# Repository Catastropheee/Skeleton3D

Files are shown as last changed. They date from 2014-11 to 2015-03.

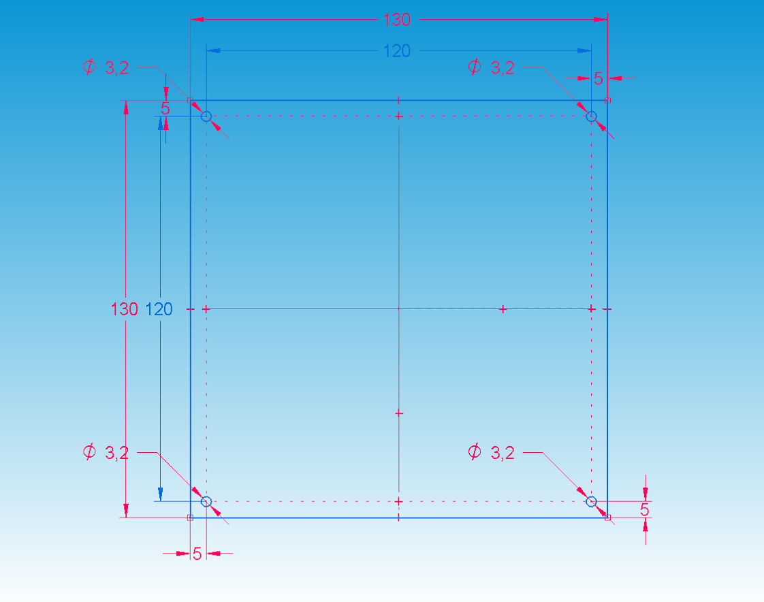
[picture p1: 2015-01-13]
STL Skeleton3D/Wood_Steel plate/Wood_Steel plate.png

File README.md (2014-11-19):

Skeleton3D
==========

Source de la petite reprap française 
Je viens vous présenter mon petit projet reprap: la skeleton 3D

L’idée a germé dans ma tête après quelques mois d’utilisation de ma prusa i3, beaucoup de personnes dans mon entourage avaient envie de voir la bécane fonctionner mais ce n’est pas super facile de transporter une i3. De plus, j’ai constaté que j’utilisais très rarement l’entière surface d’impression et que la majorité de mes print se limite à une surface de 100x100.

Après avoir cherché une petite imprimante compacte, transportable et peu chère sur le wiki, j’ai décidé d’en concevoir une répondant à mes besoins faute d’en trouver une ! 
C’est-à-dire: transportable, robuste, évolutive, peu cher mais avec des impressions de qualité !

L'union faisant la force et augmentant la créativité, j’ai travaillé avec un ami possédant aussi une i3 qui a tout de suite accroché.

Nous avons par la suite, commencé par définir :
L’architecture de la machine 
- Pièces plastiques + tiges filetés Ø8 (?€)
- Déplacement de la hotend en X et Y (course 100x100) et du plateau en Z (course 100 à 150 mm)
- Mouvements axiaux + Extrusion
- 4 moteurs NEMA 17 de 40 mm et 4kg
- 1 extruder conçu pour être compact et en directdrive

Guidage axiaux :
- Classique avec des LM8UU

Hotend :
- Aluhotend 1.75mm (en cours de test)

Alimentation :
- 72W de pc portable

Améliorations apportées au prototype :
->	Augmentation de la surface de guidage (2xLM8uu) au niveau de l’effort moteur (X et Y) pour supprimer le risque d’arc boutement
->	Augmentation de la surface de guidage du plateau Z (3x LM8uu) pour limiter la flexion
->	Augmentation de la surface de guidage de la hotend (4 x LM8uu) pour supprimer les jeux
->	Mise en place d’un plateau acier galva 15/10
->	Fixation par vis des endstop intégré aux pièces plastiques
->	Calibrage Z via une vis M4 réglable

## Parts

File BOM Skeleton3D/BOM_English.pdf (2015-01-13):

N° | Qty. | STL files ?
1 | 8 | N° | Qty. | STL files ? | N° | Qty. | STL files ?
2 | 2 | 1 | 1 | .stl | 1 | 3
3 | 1 | 2 | 1 | | 2 | 1 | .stl
4 | 3 | 3 | 1 | .stl | 3 | 1
5 | 1 | 4 | 1 | | 4 | 1 | .stl
6 | 4 | .stl | 5 | 1 | .stl
7 | 1 | .stl | 6 | 2
8 | 1 | .stl | 7 | 1
9 | 1 | .stl | 8 | 3
10 | 4 | .stl | 9 | 1
11 | 4 | 10 | 1
12 | 4 | 11 | 1
13 | 1 | .stl | 12 | 1
14 | 1 | .stl | 13 | 1
15 2
16 2
17 | 2 | N° | Qty. | STL files ?
18 | 1 | .stl | 1 | 2
19 | 55 | 2 | 3
20 | 1 | .stl | 3 | 1
21 | 1 | 4 | 1 | .stl
22 | 3 | 5 | 1
23 22 | | Socket cap screw - M3x10
24 6 | | Socket cap screw - M3x20
25 10 | | M3 nuts
26 1 | | Steel plate
27 1 | | Ramps 1.4/Arduino
28 | 4 | Ramps tab | .stl
29 2 | | Sous-ensemble glissière (see Page 2)
30 | 1 | Support hotend | .stl
31 1 | | Sous-ensemble Extruder (See page 3)
32 3 | | M4 nuts
33 | 1 | Mouting clip motor E | .stl
34 1 | | Socket cap screw - M4x10
35 | 1 | Belt guidance X | .stl
36 | 1 | Belt guidance Y | .stl
37 5 | | Socket cap screw - M3x30
38 1 | | Socket cap screw - M3x40
39 1 | | Long M5 nuts
40 11 | | M3 nuts
41 1 | | Fan 40x40x10
42 1 | | Fan 30x30x10
43 | 1 | Bec cooling | .stl
44 2 | | Inductive sensor M8 - 2mm detection
45 2 | | M8 nuts
46 | 1 | Z_support_plate_link | .stl
47 | 1 | Z_left_support_plate | .stl
48 | 1 | Z_right_support_plate | .stl
49 | 1 | Plate_pusher | .stl
50 1 | | Socket cap screw - M4x10
51 8 | | LM8UU
52 4 | | Tie wrap
53 | 2 | Steel/PLA triangle | .stl

NEMA 17 - 4kg torque - 40mm GT2 pulley
624zz bearing
GT2 belt - 800mm to be sure Support pulley Y
M8 nuts
Support motor X

Z_top_connector

Name

NEMA 17 - 4kg torque - 40mm Wood plate
Bottom connector
Z_motor_piece_1_2
Z_motor_piece_2_2

Top connector

Shaft coupling 5x5

Ø8 Smooth Rod - 220mm
M8 Threaded Rod - 190mm
Support motor Y
Support pulley X

Page 1

M8 Threaded Rod - 240mm | Name
Ø8 Smooth Rod - 180mm
M5 Threaded Rod - 160mm

Microswitch mechanical - 20x10mm

Aluhotend (http://reprap.org/wiki/Aluhotend)

Compact Extrudeur 1.75
Sous-ensemble Entrainement (see behind) Geared wheels
624zz bearings
Mobile party
M3 nuts

Name

M5x30 Hex screw

605zz bearings
Washer M5
MK7
Geared wheels

USE IT WITH BOM_Skeleton3D.pdf

Sous-ensemble Entrainement

Page 3
Sous-ensemble 31 : Extrudeur

Page 2
Sous-ensemble 29 : Glissière Name
LM8UU
Opposite linear guidance
Ø8 Smooth rods - 220mm
Motor linear guidance

Socket cap screw - M3x20
Socket cap screw - M3x10
Socket cap screw - M4x10
M4 nuts
Socket cap screw - M3x40

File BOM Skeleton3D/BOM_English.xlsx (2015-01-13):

USE IT WITH BOM_Skeleton3D.pdf
Page 1 |  |  |  | Page 3 |  |  |  | Page 2
N° | Qty. | Name | STL files ? | Sous-ensemble 31 : Extrudeur |  |  |  | Sous-ensemble 29 : Glissière
1 | 8 | M8 Threaded Rod - 240mm |  | N° | Qty. | Name | STL files ? | N° | Qty. | Name | STL files ?
2 | 2 | Ø8 Smooth Rod - 180mm |  | 1 | 1 | Compact Extrudeur 1.75 | .stl | 1 | 3 | LM8UU
3 | 1 | M5 Threaded Rod - 160mm |  | 2 | 1 | Sous-ensemble Entrainement (see behind) |  | 2 | 1 | Opposite linear guidance | .stl
4 | 3 | NEMA 17 - 4kg torque - 40mm |  | 3 | 1 | Geared wheels | .stl | 3 | 1 | Ø8 Smooth rods - 220mm
5 | 1 | Wood plate |  | 4 | 1 | 624zz bearings |  | 4 | 1 | Motor linear guidance | .stl
6 | 4 | Bottom connector | .stl | 5 | 1 | Mobile party | .stl
7 | 1 | Z_motor_piece_1_2 | .stl | 6 | 2 | M3 nuts
8 | 1 | Z_motor_piece_2_2 | .stl | 7 | 1 | Socket cap screw - M3x20
9 | 1 | Z_top_connector | .stl | 8 | 3 | Socket cap screw - M3x10
10 | 4 | Top connector | .stl | 9 | 1 | Socket cap screw - M4x10
11 | 4 | Ø8 Smooth Rod - 220mm |  | 10 | 1 | M4 nuts
12 | 4 | M8 Threaded Rod - 190mm |  | 11 | 1 | Socket cap screw - M3x40
13 | 1 | Support motor Y | .stl | 12 | 1 | Aluhotend (http://reprap.org/wiki/Aluhotend)
14 | 1 | Support pulley X | .stl | 13 | 1 | NEMA 17 - 4kg torque - 40mm
15 | 2 | GT2 pulley
16 | 2 | 624zz bearing |  | Sous-ensemble Entrainement
17 | 2 | GT2 belt - 800mm to be sure |  | N° | Qty. | Name | STL files ?
18 | 1 | Support pulley Y | .stl | 1 | 2 | 605zz bearings
19 | 55 | M8 nuts |  | 2 | 3 | Washer M5
20 | 1 | Support motor X | .stl | 3 | 1 | MK7
21 | 1 | Shaft coupling 5x5 |  | 4 | 1 | Geared wheels | .stl
22 | 3 | Microswitch mechanical - 20x10mm |  | 5 | 1 | M5x30 Hex screw
23 | 22 | Socket cap screw - M3x10
24 | 6 | Socket cap screw - M3x20
25 | 10 | M3 nuts
26 | 1 | Steel plate
27 | 1 | Ramps 1.4/Arduino
28 | 4 | Ramps tab | .stl
29 | 2 | Sous-ensemble glissière (see Page 2)
30 | 1 | Support hotend | .stl
31 | 1 | Sous-ensemble Extruder (See page 3)
32 | 3 | M4 nuts
33 | 1 | Mouting clip motor E | .stl
34 | 1 | Socket cap screw - M4x10
35 | 1 | Belt guidance X | .stl
36 | 1 | Belt guidance Y | .stl
37 | 5 | Socket cap screw - M3x30
38 | 1 | Socket cap screw - M3x40
39 | 1 | Long M5 nuts
40 | 11 | M3 nuts
41 | 1 | Fan 40x40x10
42 | 1 | Fan 30x30x10
43 | 1 | Bec cooling | .stl
44 | 2 | Inductive sensor M8 - 2mm detection
45 | 2 | M8 nuts
46 | 1 | Z_support_plate_link | .stl
47 | 1 | Z_left_support_plate | .stl
48 | 1 | Z_right_support_plate | .stl
49 | 1 | Plate_pusher | .stl
50 | 1 | Socket cap screw - M4x10
51 | 8 | LM8UU
52 | 4 | Tie wrap
53 | 2 | Steel/PLA triangle | .stl

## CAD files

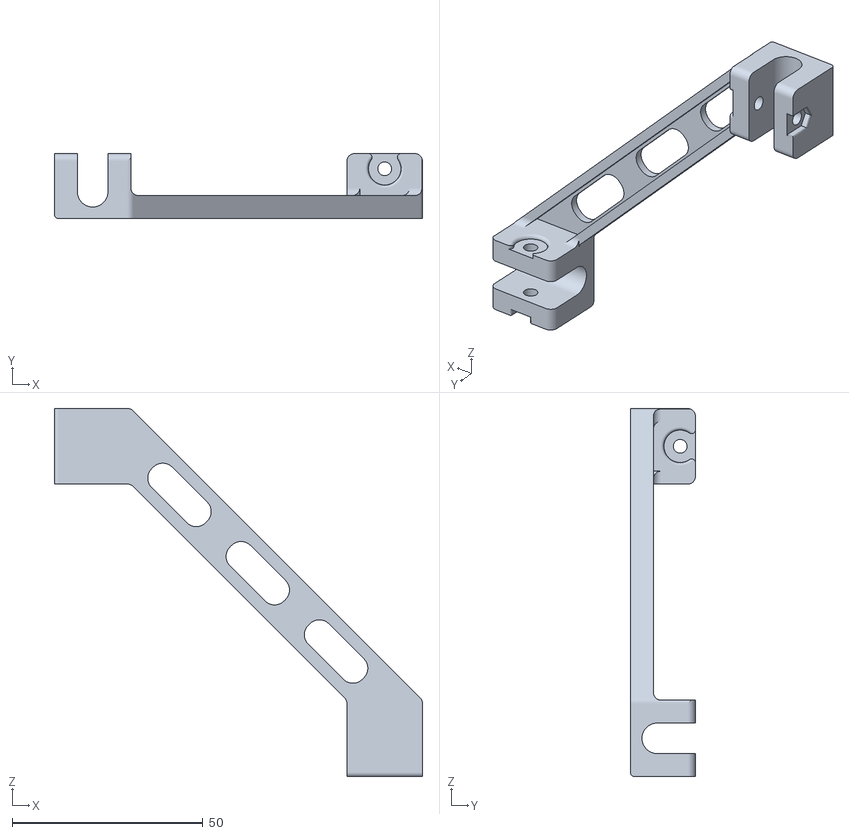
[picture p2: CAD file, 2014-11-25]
STL Skeleton3D/PLA triangle/PLA triangle.stl
96.4 x 17.0 x 96.4

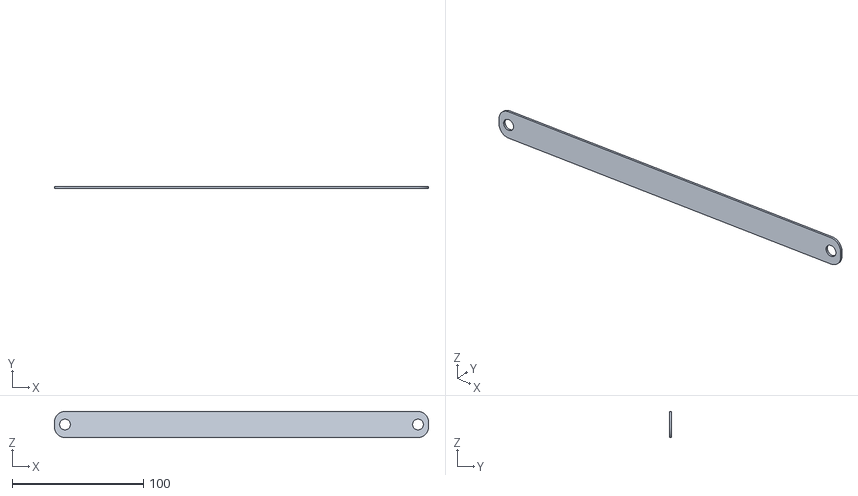
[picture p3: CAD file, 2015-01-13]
STL Skeleton3D/Steel triangle/Steel triangle.stl
285.0 x 1.50 x 20.0

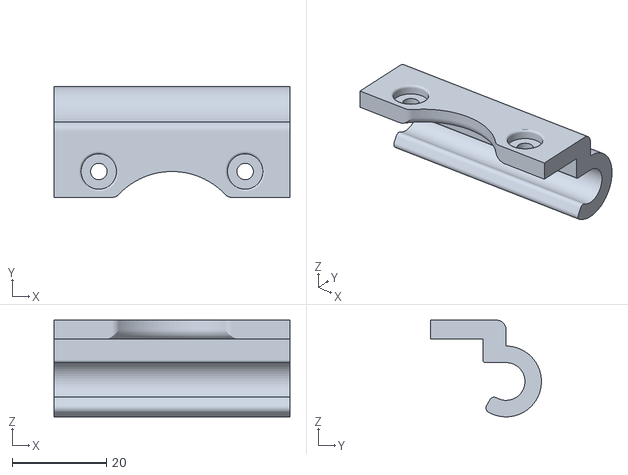
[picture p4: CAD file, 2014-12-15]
STL Skeleton3D/STL axe Z/Z_motor_piece_2_2.stl
50.0 x 23.5 x 20.5

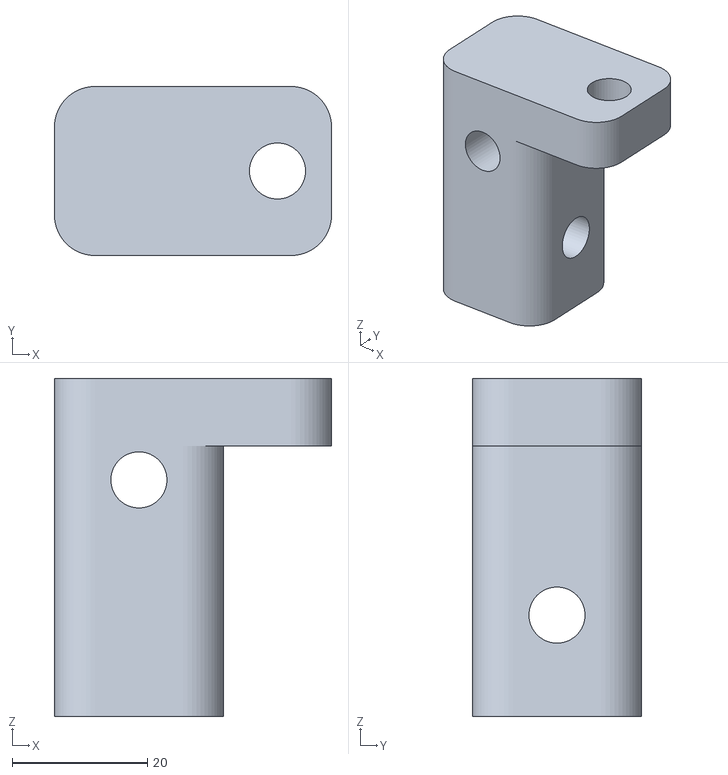
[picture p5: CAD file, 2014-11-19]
STL Skeleton3D/STL connectors/Bottom connector.stl
41.0 x 25.0 x 50.0

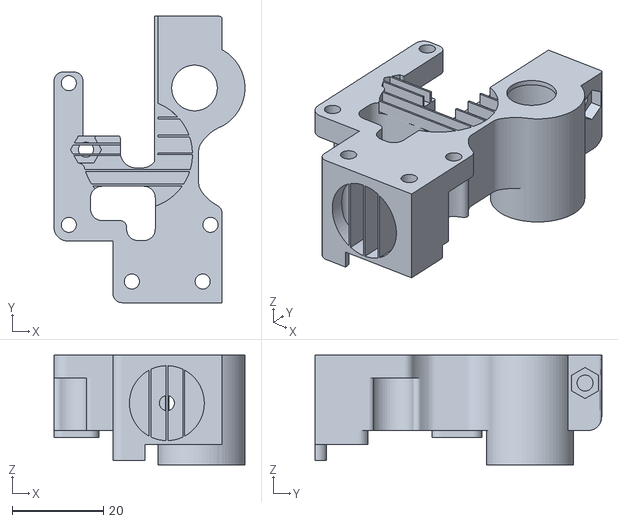
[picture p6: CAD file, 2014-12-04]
STL Skeleton3D/STL Extrudeur/Extrudeur pour thingiverse/Compact Extruder Ø3mm only with support.stl
41.8 x 62.7 x 24.0

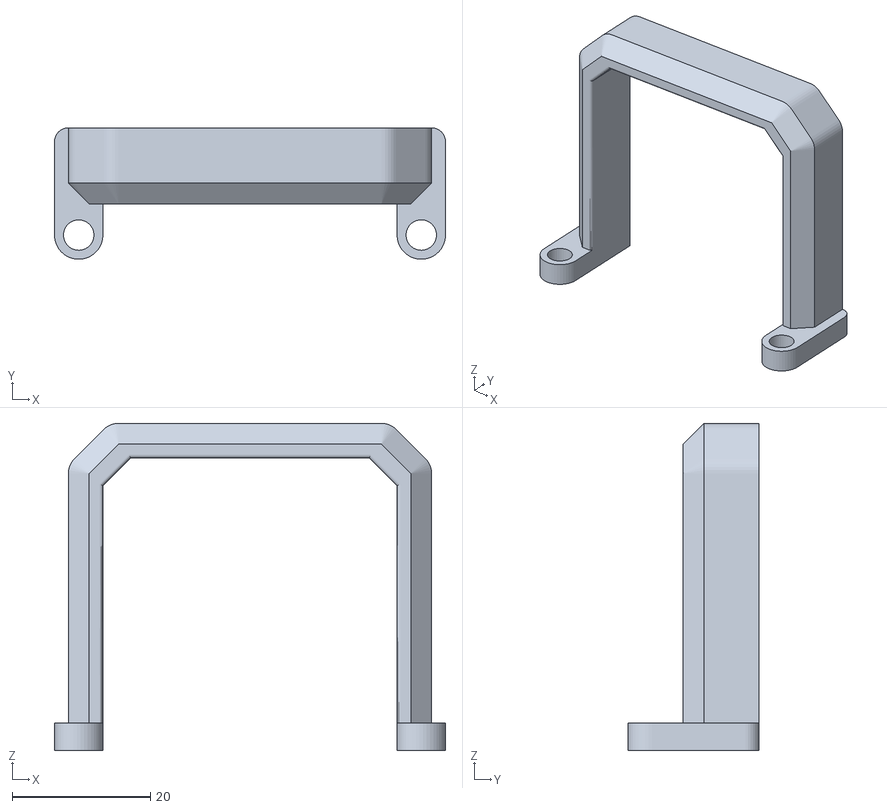
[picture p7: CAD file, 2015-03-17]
STL Skeleton3D/STL Extrudeur/Mouting clip motor E.stl
56.5 x 19.0 x 47.3

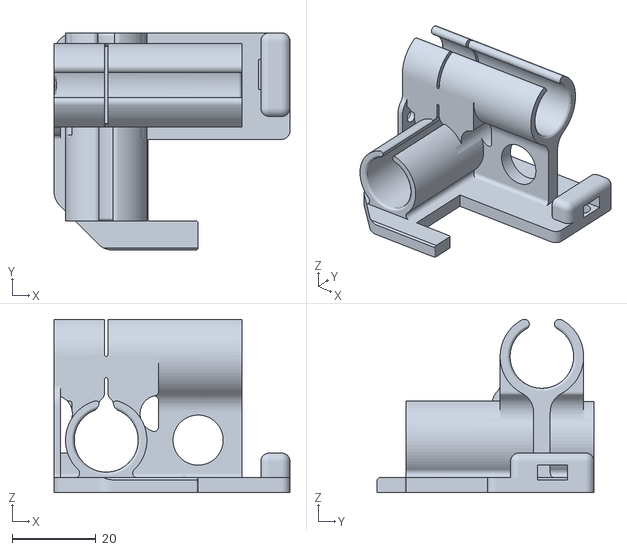
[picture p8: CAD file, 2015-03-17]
STL Skeleton3D/Support hotend.stl
56.5 x 52.0 x 41.5

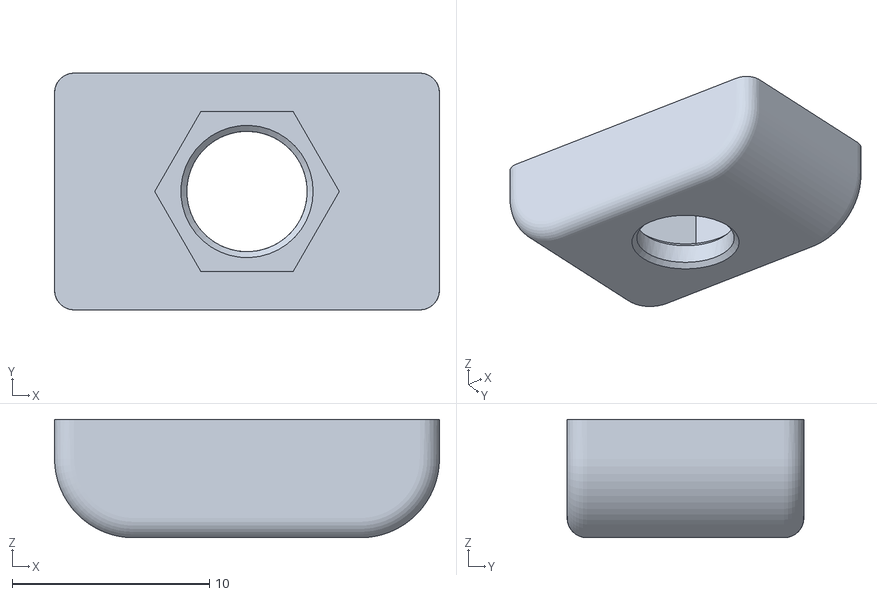
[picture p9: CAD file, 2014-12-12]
STL Skeleton3D/STL axe Z/Plate_pusher.stl
19.5 x 12.0 x 6.00

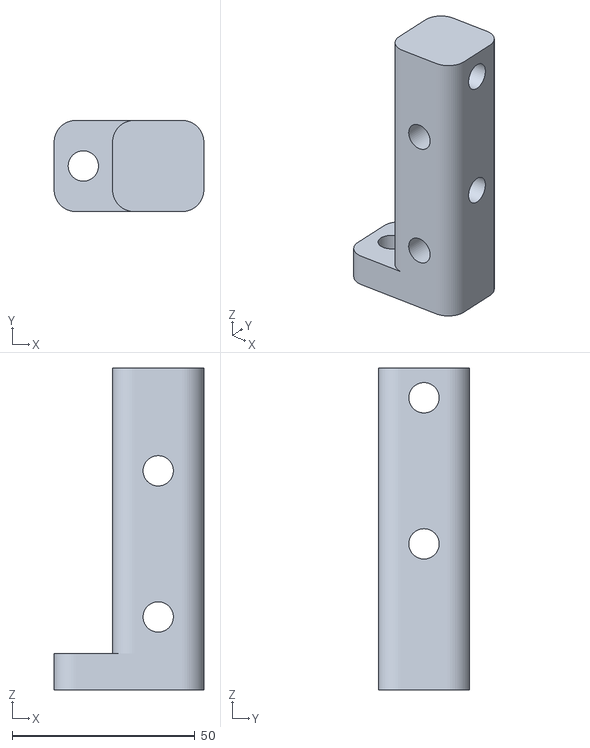
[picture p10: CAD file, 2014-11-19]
STL Skeleton3D/STL connectors/Top connector.stl
41.0 x 25.0 x 88.2

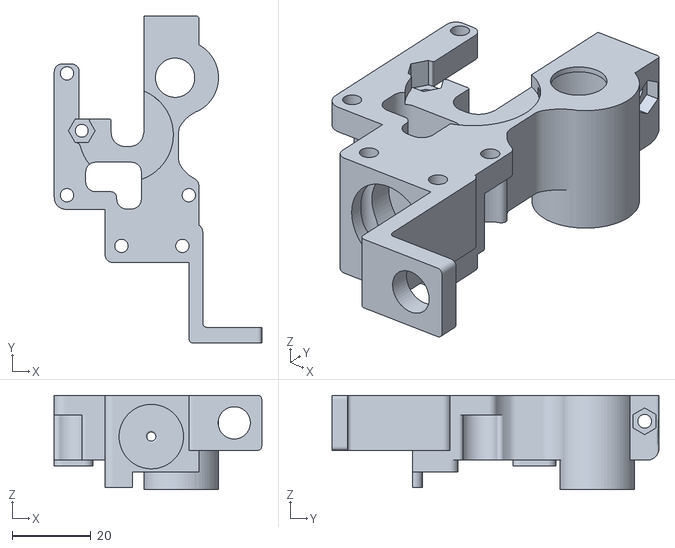
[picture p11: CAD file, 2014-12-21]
STL Skeleton3D/STL Extrudeur/Compact Extruder 1.75 without support.stl
52.8 x 83.2 x 24.0

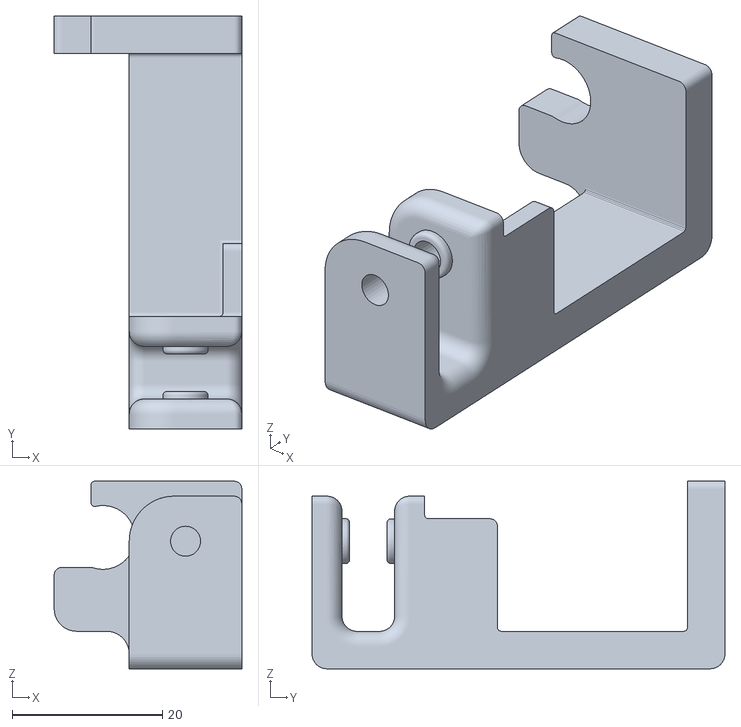
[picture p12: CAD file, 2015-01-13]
STL Skeleton3D/Support pulley X.stl
25.0 x 55.0 x 25.0

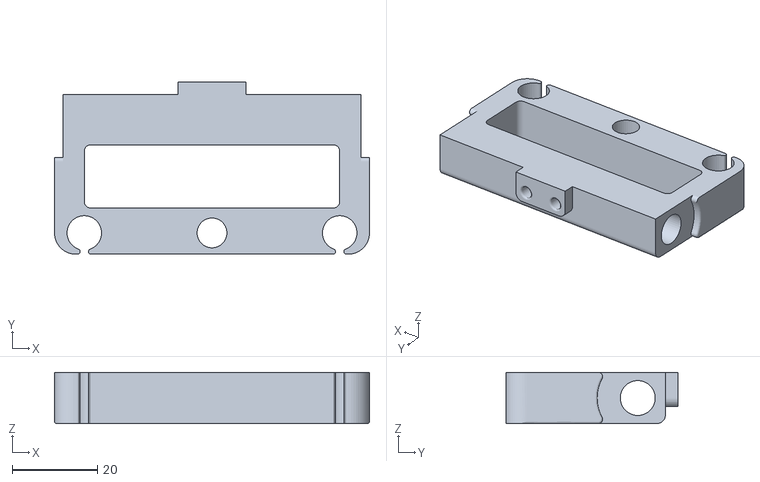
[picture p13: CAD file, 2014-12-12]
STL Skeleton3D/STL axe Z/Z_top_connector.stl
74.0 x 40.5 x 12.0

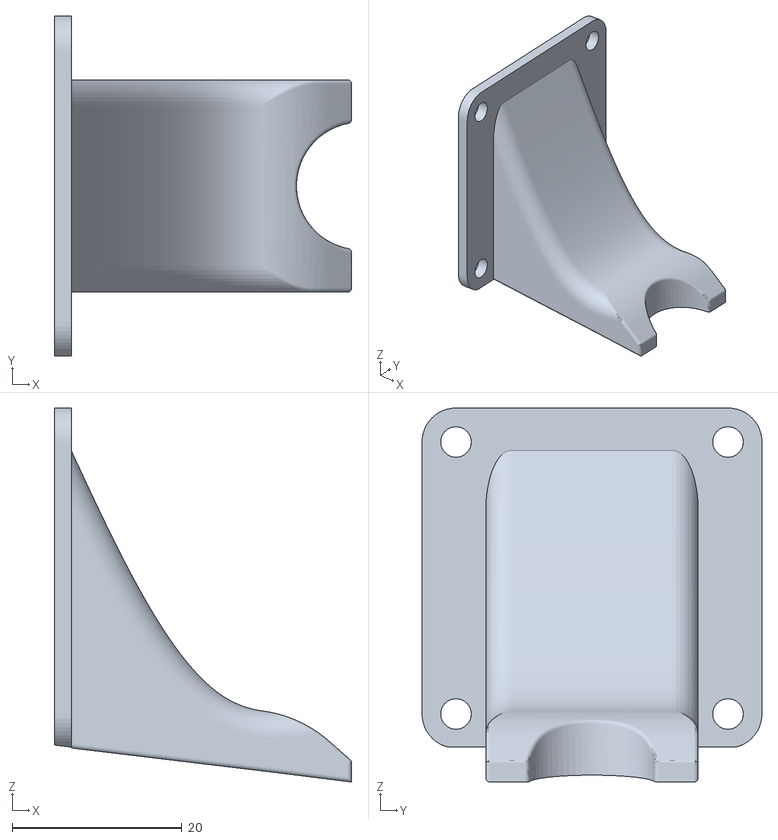
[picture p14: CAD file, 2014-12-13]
STL Skeleton3D/STL Extrudeur/Bec cooling.stl
35.0 x 40.0 x 44.0

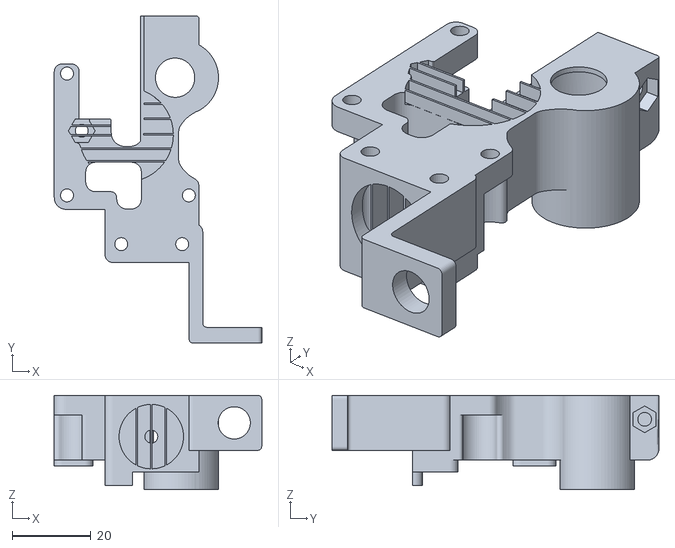
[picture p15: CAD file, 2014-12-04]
STL Skeleton3D/STL Extrudeur/Extrudeur pour thingiverse/Compact Extruder Ø3mm with sensor with support.stl
52.8 x 83.2 x 24.0

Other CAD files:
STL Skeleton3D/STL Extrudeur/Extrudeur pour thingiverse/Compact Extruder Ø1.75mm only with support.stl
STL Skeleton3D/Support pulley Y.stl
STL Skeleton3D/Opposite linear guidance.stl
STL Skeleton3D/STL axe Z/Z_support_plate_link.stl
STL Skeleton3D/Belt guidance X.stl
STL Skeleton3D/Belt guidance Y.stl
STL Skeleton3D/Motor linear guidance.stl
STL Skeleton3D/Ramps tab.stl
STL Skeleton3D/STL Extrudeur/Extrudeur pour thingiverse/Compact Extruder Ø1.75mm with sensor with support.stl
STL Skeleton3D/STL Extrudeur/Geared wheels.stl
STL Skeleton3D/STL Extrudeur/Mobile party.stl
STL Skeleton3D/STL axe Z/Z_left_support_plate.stl
STL Skeleton3D/STL axe Z/Z_motor_piece_1_2.stl
STL Skeleton3D/STL axe Z/Z_right_support_plate.stl
STL Skeleton3D/Steel triangle/Steel triangle.dxf
STL Skeleton3D/Support motor X.stl
STL Skeleton3D/Support motor Y.stl

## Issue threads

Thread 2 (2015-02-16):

Wrong screw for extruder part 11?

crundy, 2015-02-16:
We're currently putting together a Skeleton3D, but noticed that an M4x10 screw is not long enough to fit through the part "Mobile party.stl". I did take photos but managed to lose them in a phone disaster, but if you measure the space in the STL file above you can see it's 11.5mm, and a M4 20 would be too long and would press against the motor.

Screencap: http://crundyjunk.s3.amazonaws.com/MobilePartyLength.png

Could you double check and see if either we're doing something wrong or if indeed the screw part number is wrong?

P.S. The part numbers for the extruder page do not match between the full BoM and the English translation spreadsheet (e.g. 11 in the BoM is the M4x10 screw above, but in the English BoM 11 is an M3x40). Minor issues but thought you should know.

Catastropheee, 2015-02-16:
Hi,

Thank you for your remark.
You're right, M4x10 is not the right screw for the "Mobile party". I use an
M4x16.

I will update the BOM soon!

2015-02-16 12:05 GMT+01:00 crundy <notifications@github.com>:

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

crundy, 2015-02-16:
Thanks!

Closed 2015-02-16.

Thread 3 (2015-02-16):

Unnecessary splitting of parts?

crundy, 2015-02-16:
Is there a particular reason why Plate_pusher.stl is separate from Z_support_plate_link.stl? lowering of the Z axis seems to by gravity only, as the plate pusher is not affixed to the Z support plate link, which generally wouldn't cause problems, but if a bearing got a stiff it could cause issues. Surely if you integrated the two parts so that the nut was fixed to the Z support plate link directly then you would have a more stable plate and less risk of the plate not lowering?

Catastropheee, 2015-02-16:
It has been designed to uncouple guidance and traction which normally cause wobble.

" but if a bearing got a stiff it could cause issues" Which bearing ?

crundy, 2015-02-16:
Fair enough. I haven't yet lined everything up properly so the Z axis is a little stiff, and so I was referring to the 4 bearings in the two Z support plates. Shouldn't be a problem once it's moving smoothly up and down. I'm guessing the weight of the wood and aluminium should suffice.

Closed 2015-02-16.

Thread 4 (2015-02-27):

Fans

crundy, 2015-02-27:
Apologies, quick couple of questions about the extruder fans:

1. Re "Bec cooling.stl", this seems to be [sitting extremely close to the nozzle and hotend](http://crundyjunk.s3.amazonaws.com/Fan.PNG). Are you sure it won't melt?
2. Why are the vents for the above pointing directly at the bed? Would this rapid cooling not cause layers to peel up?
3. I note there is only one bolt holding each fan in one of the corners. Are you sure this is stable enough and won't cause the fans to wobble or slip? Fan 41 looks like it could untighten slightly and start rubbing against the X-shaft, and fan 42 looks like it could flop and smack into the Bec cooling part. I can look into some ways of adding another bolt for one of the holes or something to rest the edge on the side of the CoG unless you think it's isn't an issue?
4. Was there any reason to use two different fan sizes? Would two of the same be fine?

Thanks again for the design. We're almost there with ours.

Catastropheee, 2015-03-04:
Hi,

1. It doesn't melt on my skeleton.

2. It's a good note. We need to improve this.

3. No problem with only one bolt. You can easily add a second bolt if you
want ;). Please share if you do it!

4. If we used a 40mm fan for the coldend we will loose 10mm print area!

2015-02-27 13:50 GMT+01:00 crundy <notifications@github.com>:

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

crundy, 2015-03-04:
1 & 2: OK, I'm going to leave this part off for now. I presume it isn't essential.
3: Yes you are correct, I attached the 30mm fan and it holds in place fine, although it does point downwards very slightly. Shouldn't be a problem though.
4: Yup, my bad.

Closed 2015-03-04.

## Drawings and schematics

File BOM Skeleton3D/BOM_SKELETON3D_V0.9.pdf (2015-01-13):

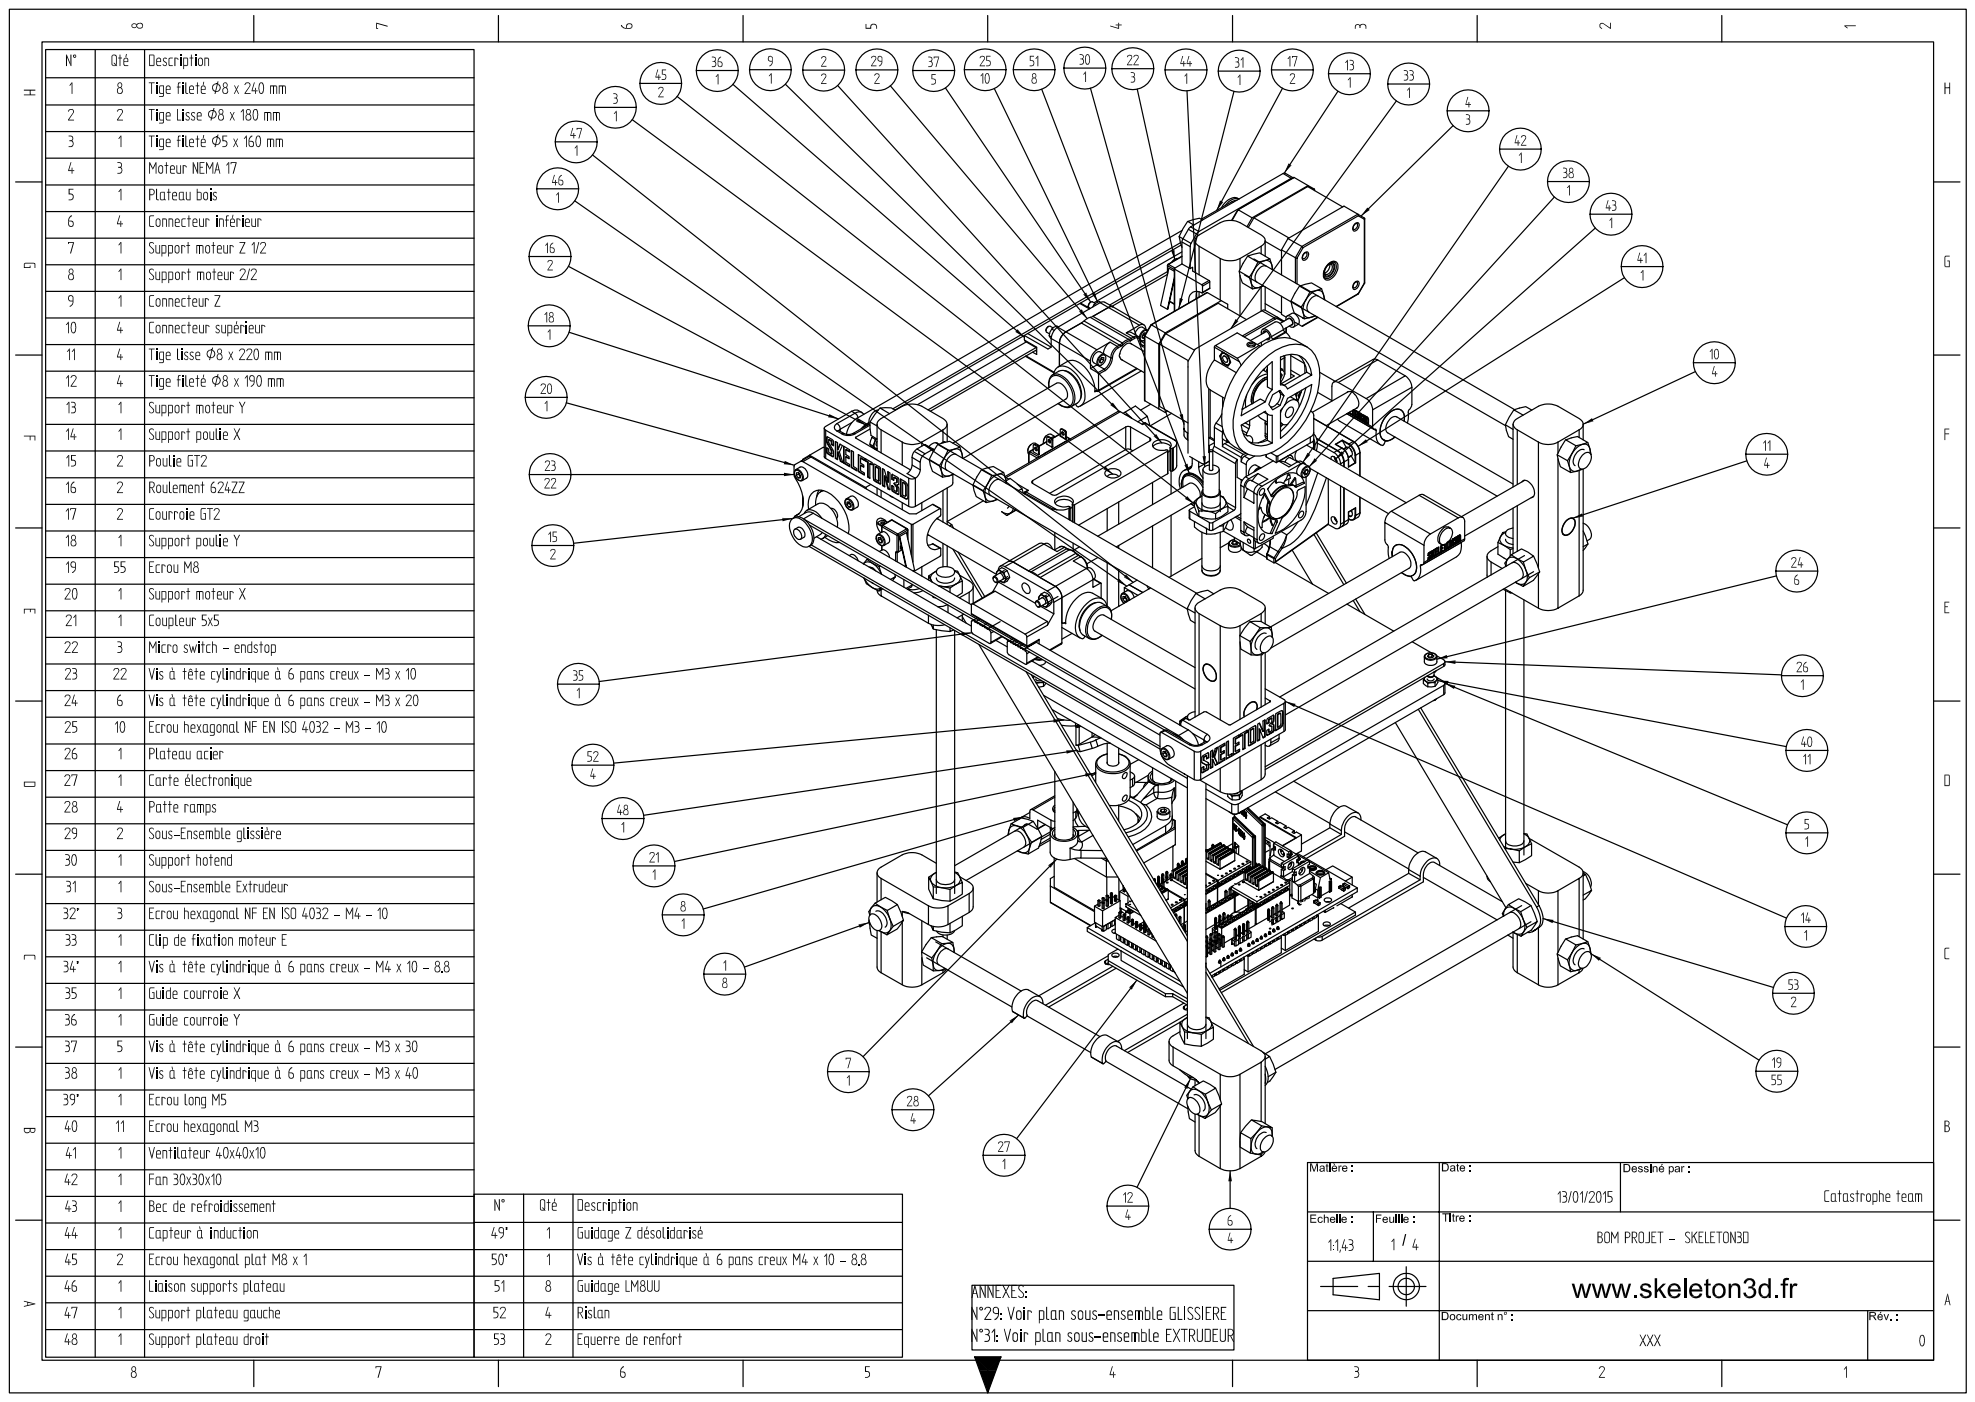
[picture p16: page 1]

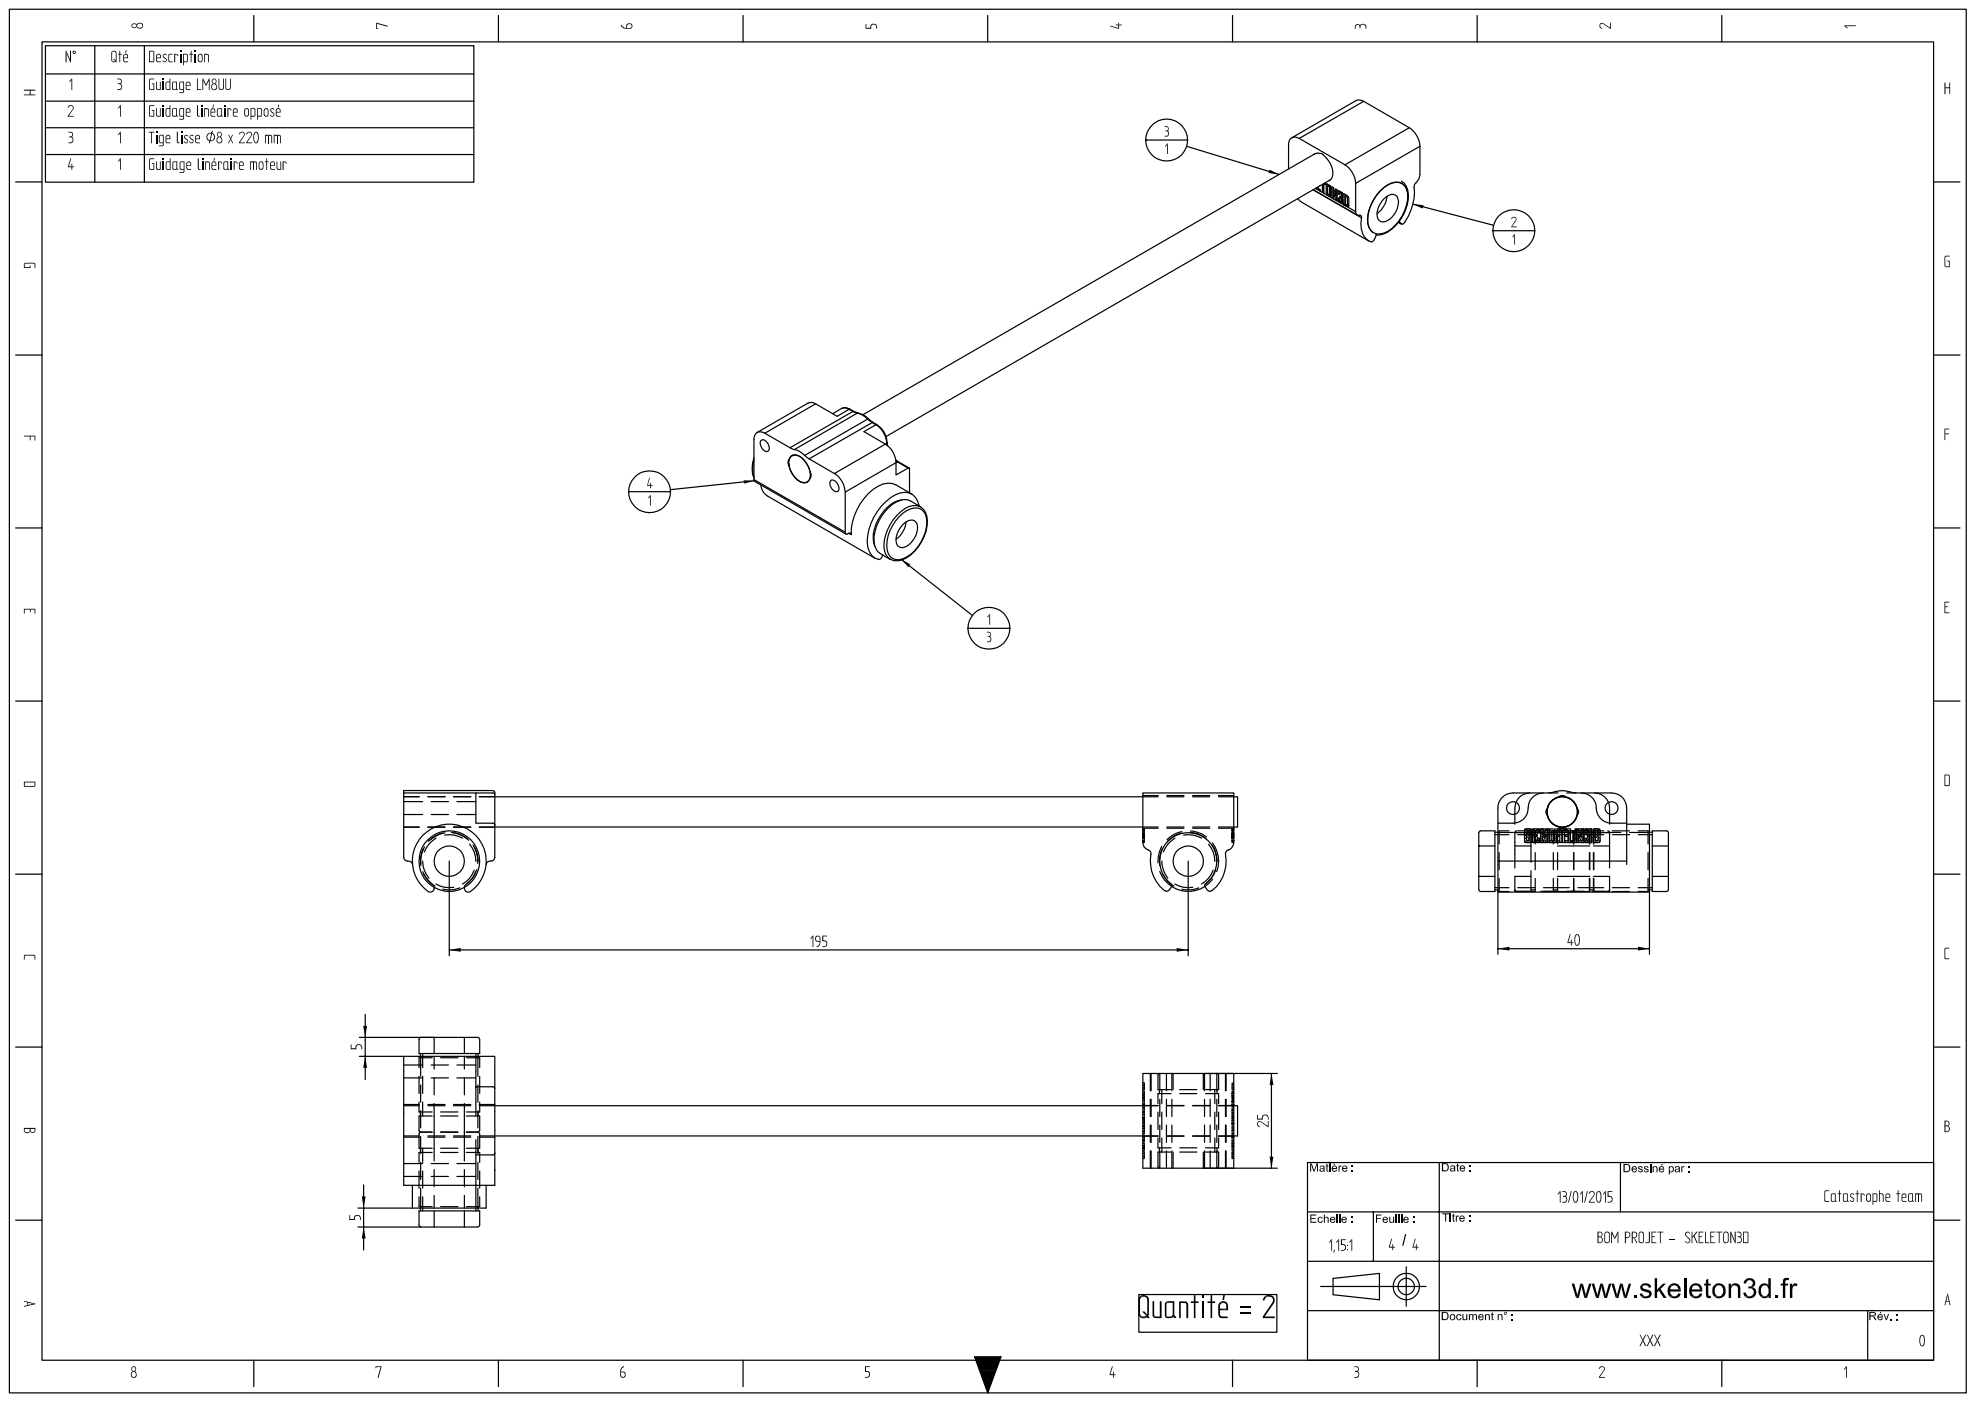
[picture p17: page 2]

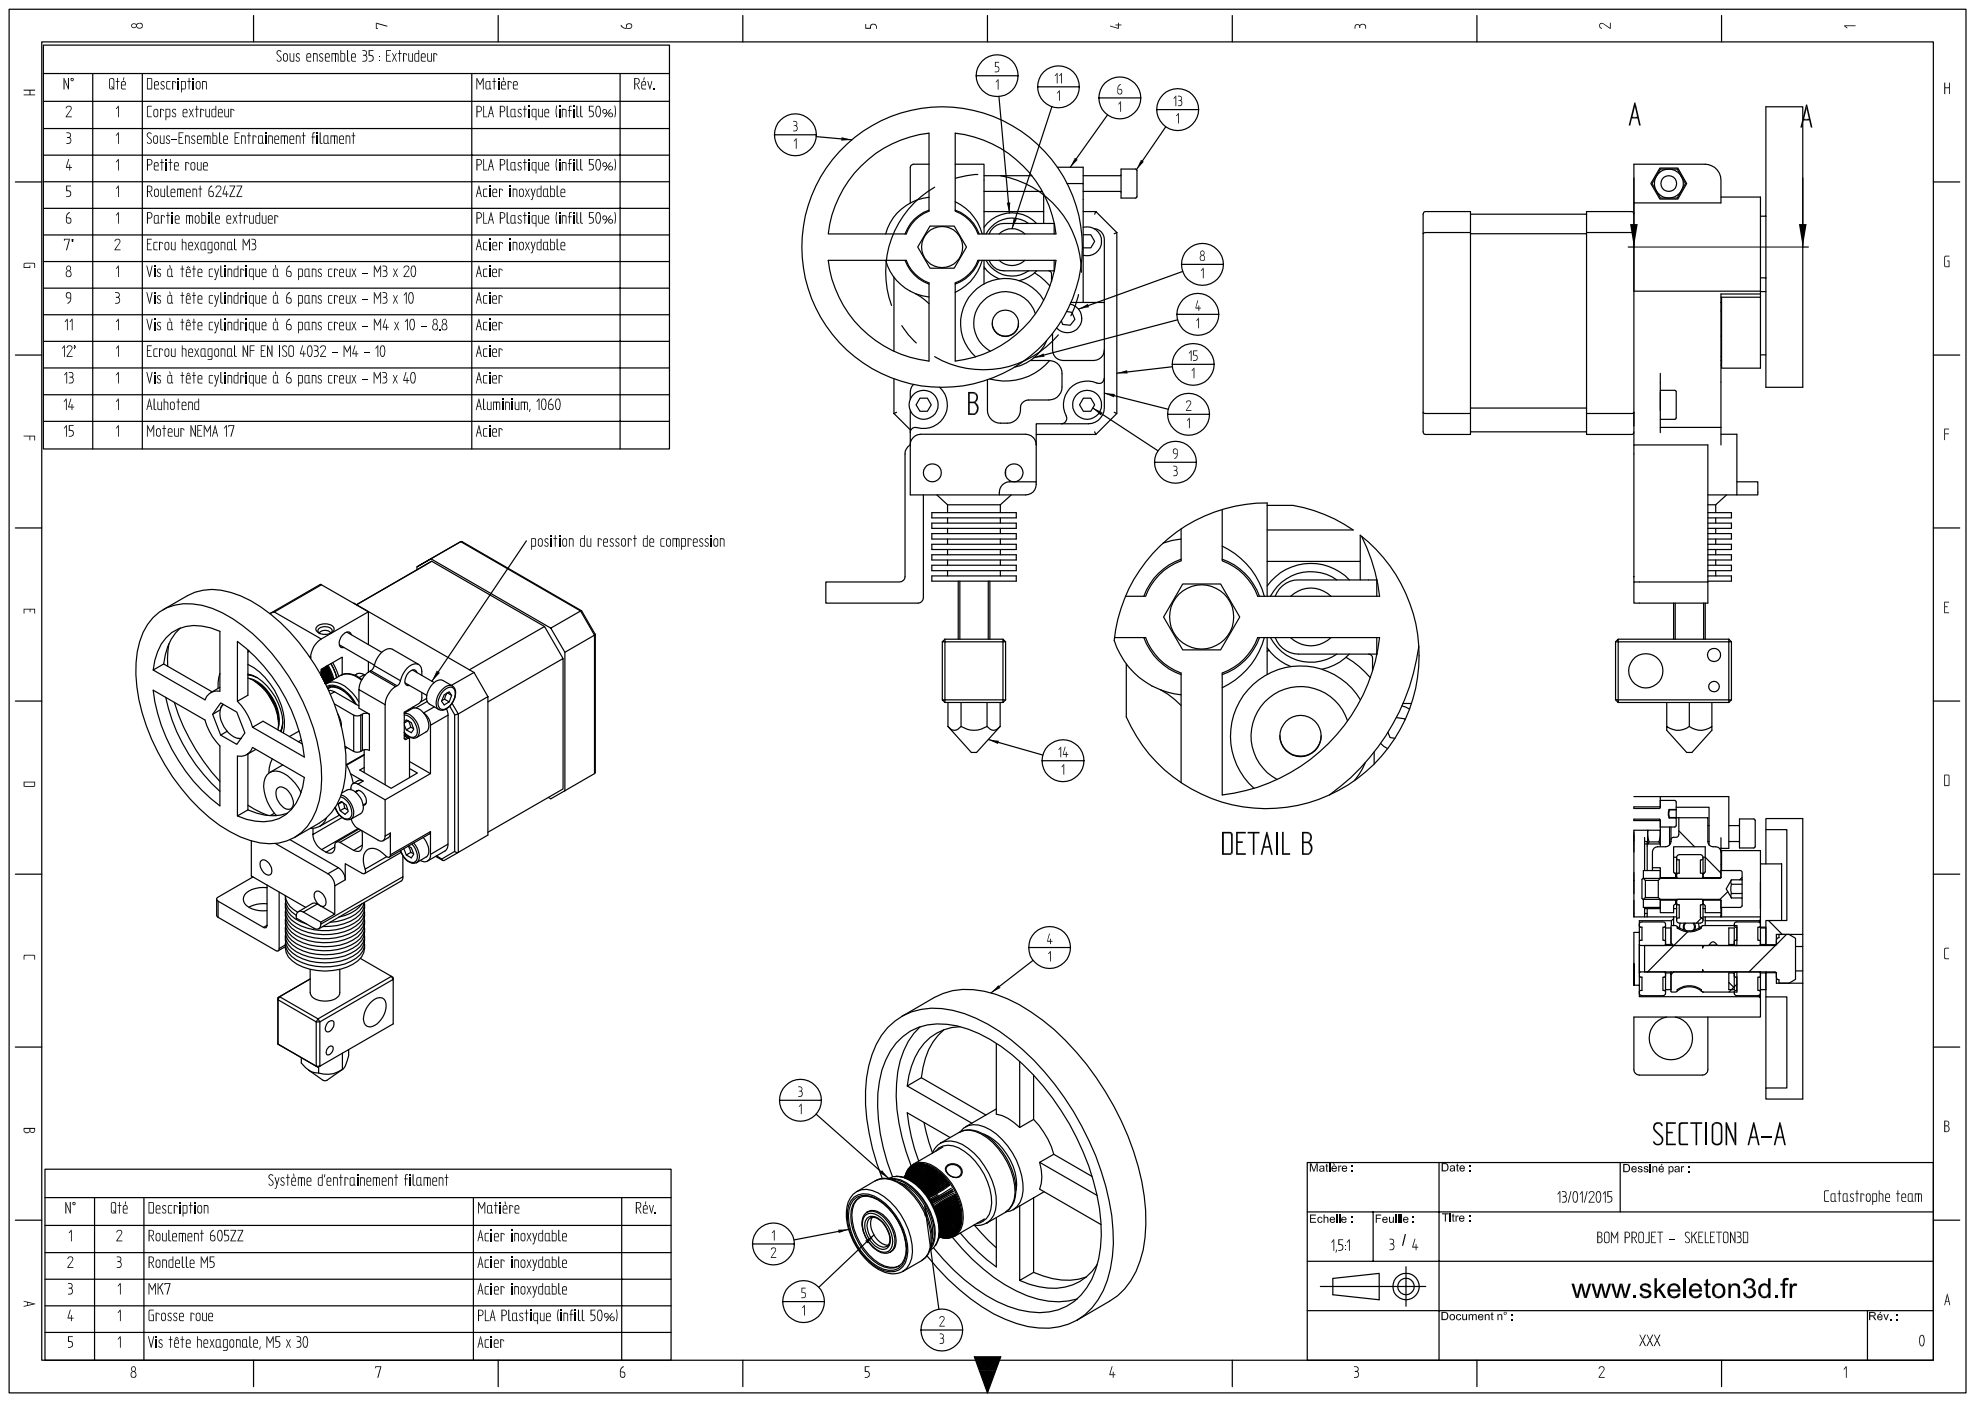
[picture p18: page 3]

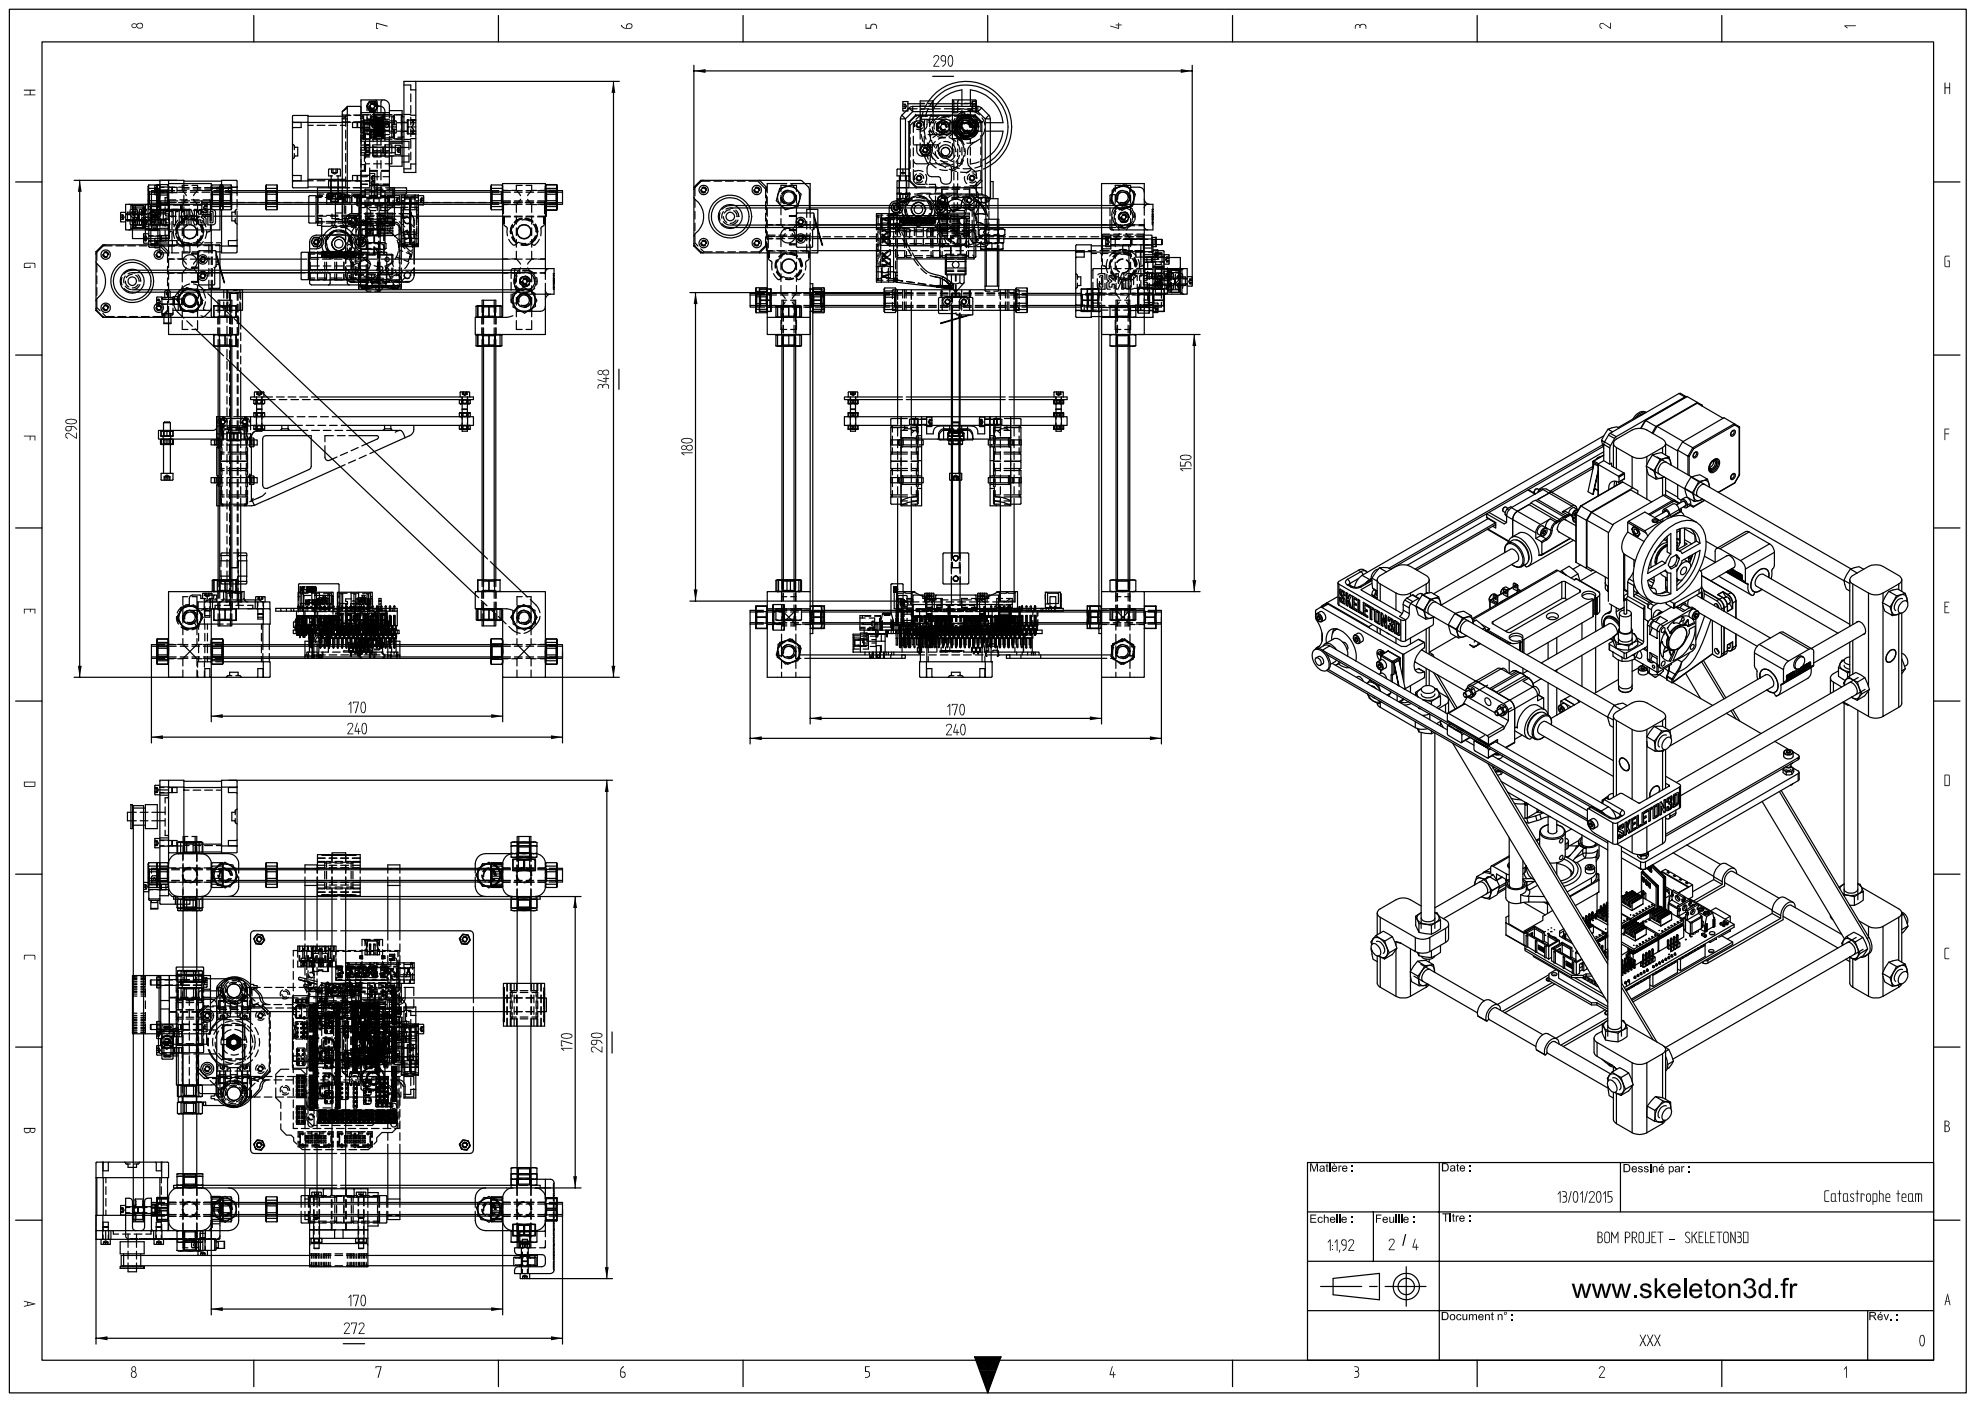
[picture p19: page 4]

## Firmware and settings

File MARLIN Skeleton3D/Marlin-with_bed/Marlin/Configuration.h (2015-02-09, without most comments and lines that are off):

#define CONFIGURATION_H
#define STRING_VERSION_CONFIG_H __DATE__ " " __TIME__ // build date and time
#define STRING_CONFIG_H_AUTHOR "(none, default config)" // Who made the changes.
#define SERIAL_PORT 0
#define BAUDRATE 250000
#define MOTHERBOARD 33
#define EXTRUDERS 1
#define POWER_SUPPLY 1
#define TEMP_SENSOR_0 10
#define TEMP_SENSOR_1 0
#define TEMP_SENSOR_2 0
#define TEMP_SENSOR_BED 11
#define MAX_REDUNDANT_TEMP_SENSOR_DIFF 10
#define TEMP_RESIDENCY_TIME 10  // (seconds)
#define TEMP_HYSTERESIS 3       // (degC) range of +/- temperatures considered "close" to the target one
#define TEMP_WINDOW     1       // (degC) Window around target to start the residency timer x degC early.
#define HEATER_0_MINTEMP 5
#define HEATER_1_MINTEMP 5
#define HEATER_2_MINTEMP 5
#define BED_MINTEMP 5
#define HEATER_0_MAXTEMP 240
#define HEATER_1_MAXTEMP 240
#define HEATER_2_MAXTEMP 240
#define BED_MAXTEMP 110
#define PIDTEMP
#define BANG_MAX 255 // limits current to nozzle while in bang-bang mode; 255=full current
#define PID_MAX 255 // limits current to nozzle while PID is active (see PID_FUNCTIONAL_RANGE below); 255=full current
  #define PID_FUNCTIONAL_RANGE 10 // If the temperature difference between the target temperature and the actual temperature
  #define PID_INTEGRAL_DRIVE_MAX 255  //limit for the integral term
  #define K1 0.95 //smoothing factor within the PID
  #define PID_dT ((OVERSAMPLENR * 8.0)/(F_CPU / 64.0 / 256.0)) //sampling period of the temperature routine
    #define  DEFAULT_Kp 22.2
    #define  DEFAULT_Ki 1.08
    #define  DEFAULT_Kd 114
#define MAX_BED_POWER 255 // limits duty cycle to bed; 255=full current
#define PREVENT_DANGEROUS_EXTRUDE
#define PREVENT_LENGTHY_EXTRUDE
#define EXTRUDE_MINTEMP 170
#define EXTRUDE_MAXLENGTH (X_MAX_LENGTH+Y_MAX_LENGTH) //prevent extrusion of very large distances.
#define ENDSTOPPULLUPS // Comment this out (using // at the start of the line) to disable the endstop pullup resistors
  #define ENDSTOPPULLUP_XMAX
  #define ENDSTOPPULLUP_YMAX
  #define ENDSTOPPULLUP_ZMAX
  #define ENDSTOPPULLUP_XMIN
  #define ENDSTOPPULLUP_YMIN
  #define ENDSTOPPULLUP_ZMIN
const bool X_MIN_ENDSTOP_INVERTING = false; // set to true to invert the logic of the endstop.
const bool Y_MIN_ENDSTOP_INVERTING = false; // set to true to invert the logic of the endstop.
const bool Z_MIN_ENDSTOP_INVERTING = false; // set to true to invert the logic of the endstop.
const bool X_MAX_ENDSTOP_INVERTING = true; // set to true to invert the logic of the endstop.
const bool Y_MAX_ENDSTOP_INVERTING = true; // set to true to invert the logic of the endstop.
const bool Z_MAX_ENDSTOP_INVERTING = true; // set to true to invert the logic of the endstop.
#if defined(COREXY) && !defined(DISABLE_MAX_ENDSTOPS)
  #define DISABLE_MAX_ENDSTOPS
#endif
#define X_ENABLE_ON 0
#define Y_ENABLE_ON 0
#define Z_ENABLE_ON 0
#define E_ENABLE_ON 0 // For all extruders
#define DISABLE_X false
#define DISABLE_Y false
#define DISABLE_Z false
#define DISABLE_E false // For all extruders
#define DISABLE_INACTIVE_EXTRUDER true //disable only inactive extruders and keep active extruder enabled
#define INVERT_X_DIR true    // for Mendel set to false, for Orca set to true
#define INVERT_Y_DIR false   // for Mendel set to true, for Orca set to false
#define INVERT_Z_DIR false     // for Mendel set to false, for Orca set to true
#define INVERT_E0_DIR false   // for direct drive extruder v9 set to true, for geared extruder set to false
#define INVERT_E1_DIR false    // for direct drive extruder v9 set to true, for geared extruder set to false
#define INVERT_E2_DIR false   // for direct drive extruder v9 set to true, for geared extruder set to false
#define X_HOME_DIR -1
#define Y_HOME_DIR -1
#define Z_HOME_DIR -1
#define min_software_endstops true // If true, axis won't move to coordinates less than HOME_POS.
#define max_software_endstops true  // If true, axis won't move to coordinates greater than the defined lengths below.
#define X_MAX_POS 100
#define X_MIN_POS 0
#define Y_MAX_POS 100
#define Y_MIN_POS 0
#define Z_MAX_POS 100
#define Z_MIN_POS 0
#define X_MAX_LENGTH (X_MAX_POS - X_MIN_POS)
#define Y_MAX_LENGTH (Y_MAX_POS - Y_MIN_POS)
#define Z_MAX_LENGTH (Z_MAX_POS - Z_MIN_POS)
#define ENABLE_AUTO_BED_LEVELING // Delete the comment to enable (remove // at the start of the line)
      #define ABL_PROBE_PT_1_X 25
      #define ABL_PROBE_PT_1_Y 50
      #define ABL_PROBE_PT_2_X 25
      #define ABL_PROBE_PT_2_Y 20
      #define ABL_PROBE_PT_3_X 60
      #define ABL_PROBE_PT_3_Y 20
  #define X_PROBE_OFFSET_FROM_EXTRUDER 20
  #define Y_PROBE_OFFSET_FROM_EXTRUDER 0
  #define Z_PROBE_OFFSET_FROM_EXTRUDER 0
  #define Z_RAISE_BEFORE_HOMING 5       // (in mm) Raise Z before homing (G28) for Probe Clearance.
  #define XY_TRAVEL_SPEED 8000         // X and Y axis travel speed between probes, in mm/min
  #define Z_RAISE_BEFORE_PROBING 5    //How much the extruder will be raised before traveling to the first probing point.
  #define Z_RAISE_BETWEEN_PROBINGS 5  //How much the extruder will be raised when traveling from between next probing points
  #define Z_SAFE_HOMING   // This feature is meant to avoid Z homing with probe outside the bed area.
    #define Z_SAFE_HOMING_X_POINT (X_MAX_LENGTH/2)    // X point for Z homing when homing all axis (G28)
    #define Z_SAFE_HOMING_Y_POINT (Y_MAX_LENGTH/2)    // Y point for Z homing when homing all axis (G28)
#define MANUAL_X_HOME_POS 0
#define MANUAL_Y_HOME_POS 0
#define MANUAL_Z_HOME_POS 0
#define NUM_AXIS 4 // The axis order in all axis related arrays is X, Y, Z, E
#define HOMING_FEEDRATE {50*60, 50*60, 2*60, 0}  // set the homing speeds (mm/min)
#define DEFAULT_AXIS_STEPS_PER_UNIT   {79.799,79.799,3920.783,533.2}  // default steps per unit for Ultimaker
#define DEFAULT_MAX_FEEDRATE          {500, 500, 3, 25}    // (mm/sec)
#define DEFAULT_MAX_ACCELERATION      {2500,2500,20,10000}    // X, Y, Z, E maximum start speed for accelerated moves. E default values are good for Skeinforge 40+, for older versions raise them a lot.
#define DEFAULT_ACCELERATION          800   // X, Y, Z and E max acceleration in mm/s^2 for printing moves
#define DEFAULT_RETRACT_ACCELERATION  800   // X, Y, Z and E max acceleration in mm/s^2 for retracts
#define DEFAULT_XYJERK                20.0    // (mm/sec)
#define DEFAULT_ZJERK                 0.4     // (mm/sec)
#define DEFAULT_EJERK                 5.0    // (mm/sec)
#define CUSTOM_M_CODES
  #define CUSTOM_M_CODE_SET_Z_PROBE_OFFSET 851
  #define Z_PROBE_OFFSET_RANGE_MIN -15
  #define Z_PROBE_OFFSET_RANGE_MAX -5
#define PLA_PREHEAT_HOTEND_TEMP 180
#define PLA_PREHEAT_HPB_TEMP 70
#define PLA_PREHEAT_FAN_SPEED 255   // Insert Value between 0 and 255
#define ABS_PREHEAT_HOTEND_TEMP 240
#define ABS_PREHEAT_HPB_TEMP 100
#define ABS_PREHEAT_FAN_SPEED 255   // Insert Value between 0 and 255
#define REPRAP_DISCOUNT_FULL_GRAPHIC_SMART_CONTROLLER
 #define DOGLCD
 #define U8GLIB_ST7920
 #define REPRAP_DISCOUNT_SMART_CONTROLLER
 #define ULTIPANEL
 #define NEWPANEL
  #define SDSUPPORT
  #define ULTRA_LCD
    #define LCD_WIDTH 20
    #define LCD_HEIGHT 5
#  define DEFAULT_LCD_CONTRAST 32
#define SOFT_PWM_SCALE 0
#include "Configuration_adv.h"
#include "thermistortables.h"

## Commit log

2014-11-19 publication v0.1
    Skeleton3d v0.1
    [Chariot plateau Z.stl, Clip de fixation moteur E.stl, Connecteur Z.stl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]
2014-11-22 Add BOM
2014-11-23 Name
    Add "skeleton3d" on 3 .stl
    [Guidage linéaire opposé.stl, Support poulie X.stl, support poulie Y.stl]
2014-11-25 BOM in English
    USE IT WITH BOM_Skeleton3D.pdf
2014-11-25 Bec + triangle
    [Bec de refroidissement.stl, Equerre de stabilisation.stl]
2014-11-29 Add extrudeur in 3mm
    [Extrudeur_1-75mm.stl, Extrudeur_3mm.stl]
2014-12-04 news parts
    Now the extruder come with support integred!
    [Compact Extruder Ø1.75mm only with support.stl, Compact Extruder Ø1.75mm with sensor with support.stl, Compact Extruder Ø3mm only with support.stl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]
2014-12-04 Revert "news parts"
    This reverts commit 2383504779074908fac9c1998d64f05267165ff2.
    [Compact Extruder Ø1.75mm only with support.stl, Compact Extruder Ø1.75mm with sensor with support.stl, Compact Extruder Ø3mm only with support.stl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]
2014-12-04 News extruder
    with support for printing and support for an inductive sensor
    [Compact Extruder Ø1.75mm only with support.stl, Compact Extruder Ø1.75mm with sensor with support.stl, Compact Extruder Ø3mm only with support.stl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]
2014-12-04 4-rods guidance
    [Connecteur inférieur - guide plateau.stl, Connecteur supérieur - guide plateau.stl, Guide chariot avant droit.stl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]
2014-12-12 New support plate Z
    Improvement :
    -Better support of the plate
    -Guidance and traction are now decoupled (Plate_pusher go in
    Z_support_plate_link)
    [Chariot plateau Z.stl, Connecteur Z.stl, Plate_pusher.stl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]
2014-12-13 bug fixed
    [Bec de refroidissement.stl, Support hotend.stl]
2014-12-14 big fixed
    [Support hotend.stl]
2014-12-21 English translation
    [Bec cooling.stl, Belt guidance X.stl, Belt guidance Y.stl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]
2014-12-21 Revert "bug fixed"
    This reverts commit ac45fb9d0f7b37a0c8e2cdfc563f217248e61899.
    [Support hotend.stl, Z_motor_piece_2_2.stl]
2014-12-21 Revert "Revert "bug fixed""
    This reverts commit 79ee3ed305cef4cc3ad0f6c6c740f4e244931b85.
    [Support hotend.stl, Z_motor_piece_2_2.stl]
2015-01-13 Update to V0.9
    [Equerre de stabilisation.stl, Equerre métal.dxf, Equerre métal.stl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]
2015-01-13 Update to V0.9
    Last Version
    [BOM_English.xlsx, Configuration.h, Configuration_adv.h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]
2015-02-09 Update Marlin
    [Configuration.h, Configuration_adv.h, Menu Plans.xlsx]
2015-03-17 New version
    [Mouting clip motor E.stl, Support hotend.stl]
